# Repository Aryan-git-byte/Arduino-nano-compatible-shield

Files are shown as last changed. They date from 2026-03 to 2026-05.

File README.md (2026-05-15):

# Arduino Nano Compatible Shield

## overview:
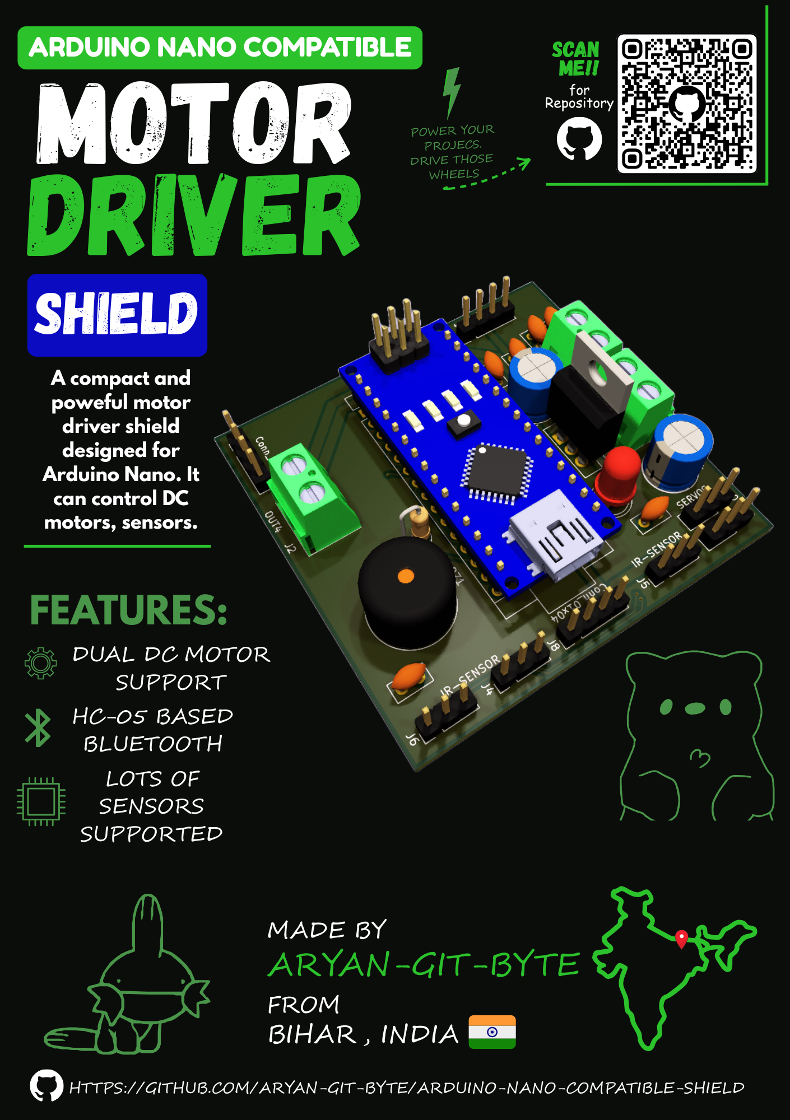
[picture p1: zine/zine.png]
zine

This project is a custom Arduino Nano compatible robotics shield designed to simplify building a 2WD robot car with integrations of many sensors such as ir sensor, ultrasonic, mpu6050 and communication device as bluetooth       
The ultimate goal is to eliminate all those messy wirings , and solderings that we do while making simple 2wd cars packed with features in affordable range.    

## Features:
- U can drive 2 motors with this shield 
- u can integrate 3 ir sensors, 1 ultrasonic sensor, 1 mpu6050, 1 HC-05, and 2 servos

## How to use:
1. insert arduino nano
2. flash the nano with the firmware(change acocrding to your need)
3. connect all the sensors, motors, u need.
4. power the board and operate it

## firmware: Basic firmware written in .ino

## PCB :
### Schematic:
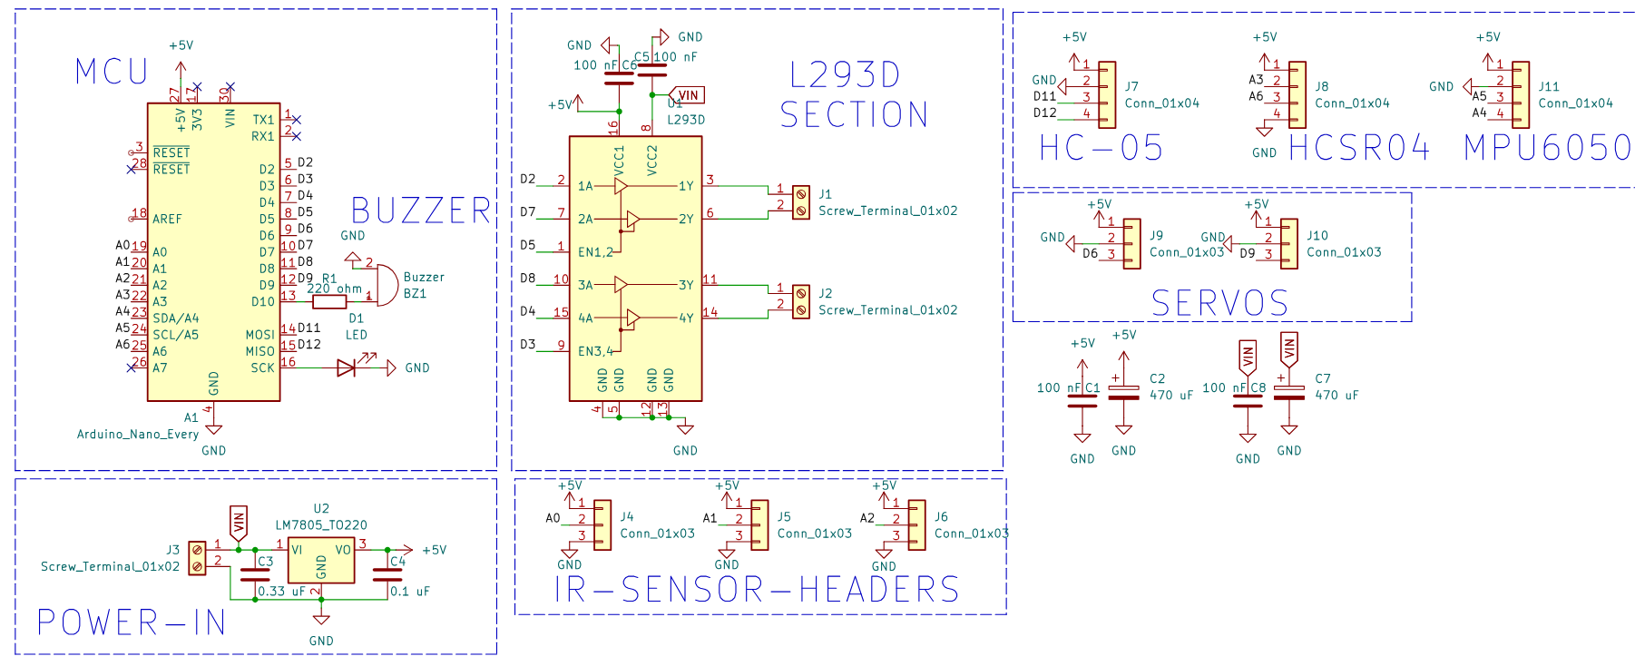
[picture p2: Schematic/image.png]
schematic


### PCB:        
top layer:
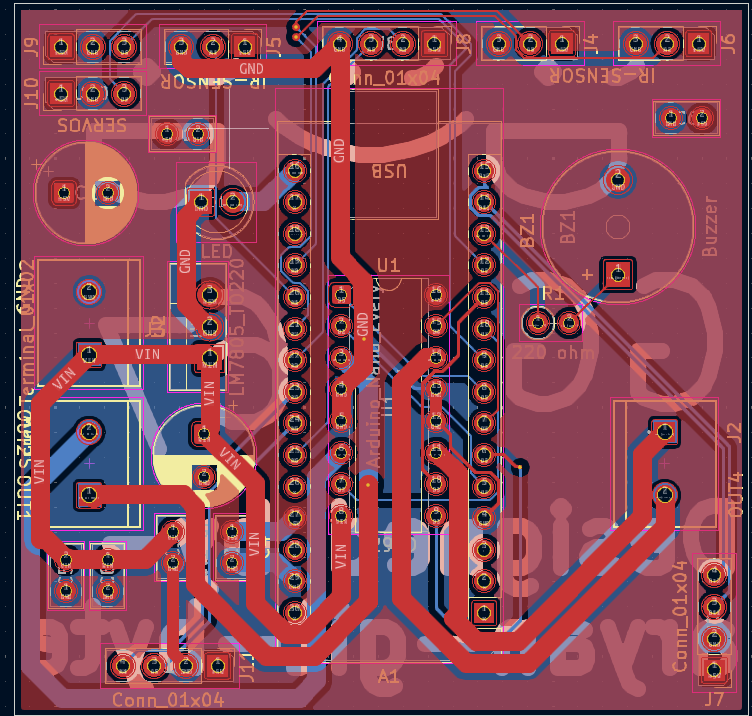
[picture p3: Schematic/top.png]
top
       
bottom layer:       
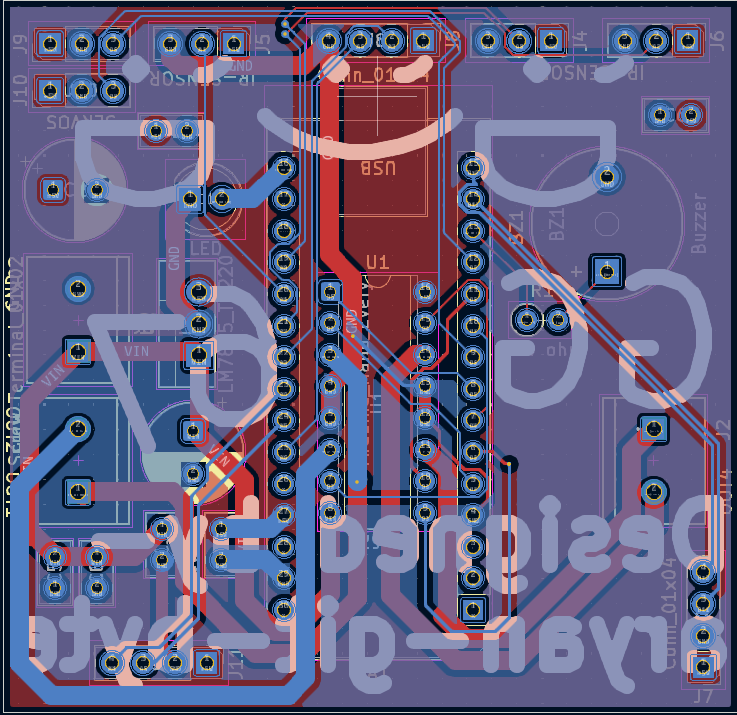
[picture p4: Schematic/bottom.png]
bottom
     
F.silkscreen:       
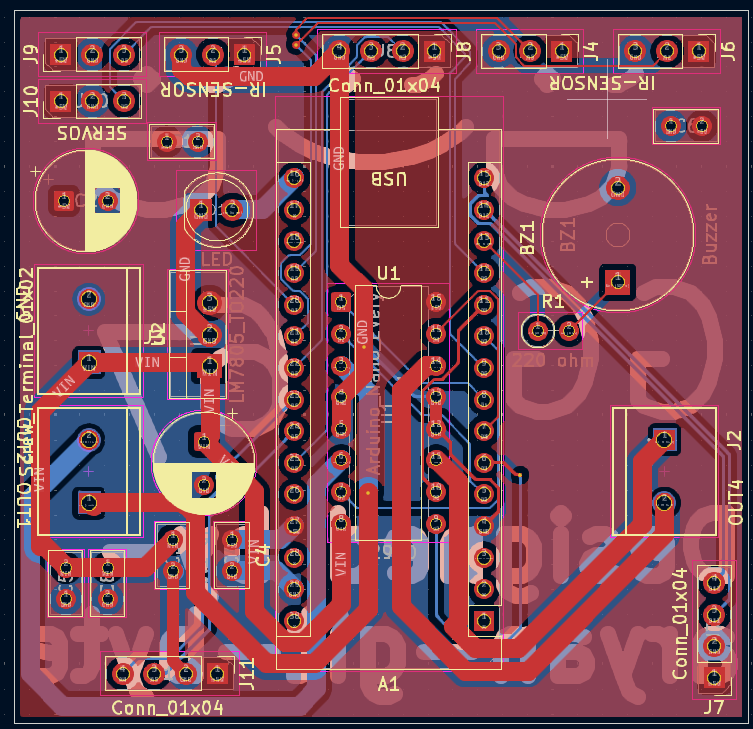
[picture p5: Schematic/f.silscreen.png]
top-silkscreen
    
B.silkscreen:
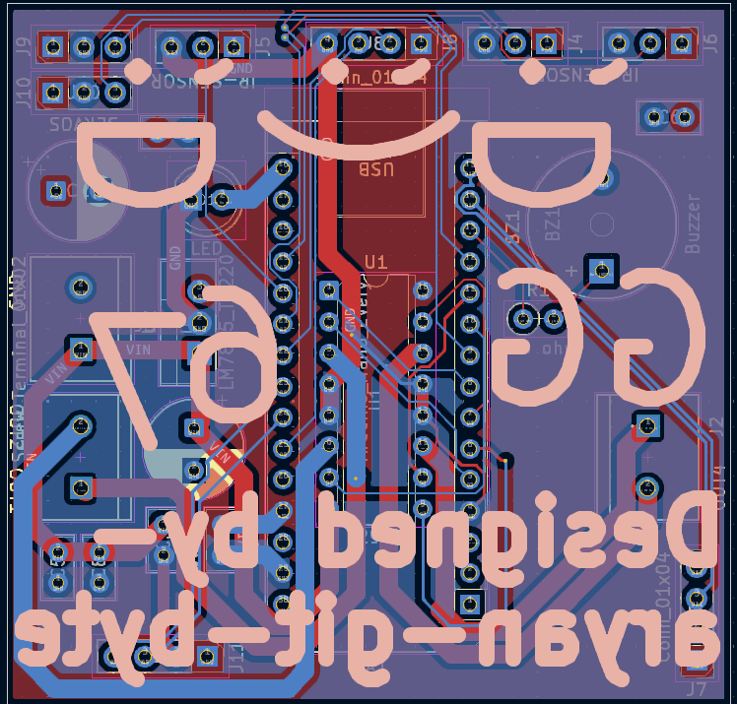
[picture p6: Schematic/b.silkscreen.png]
black-silkscreen

3d:
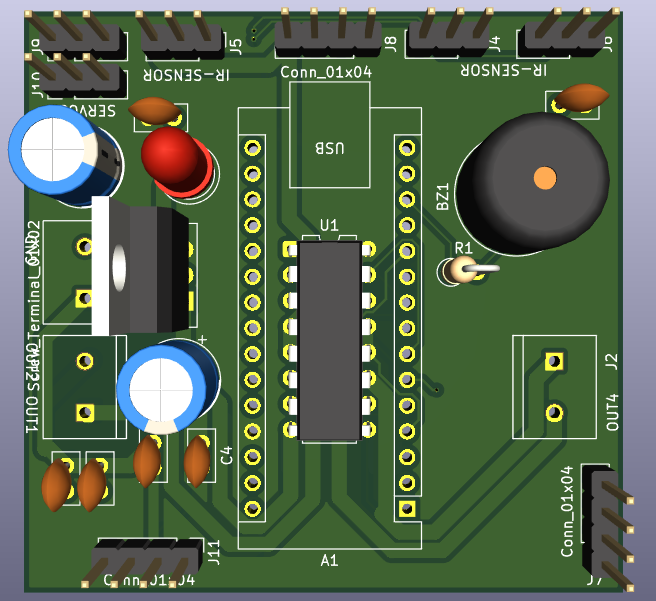
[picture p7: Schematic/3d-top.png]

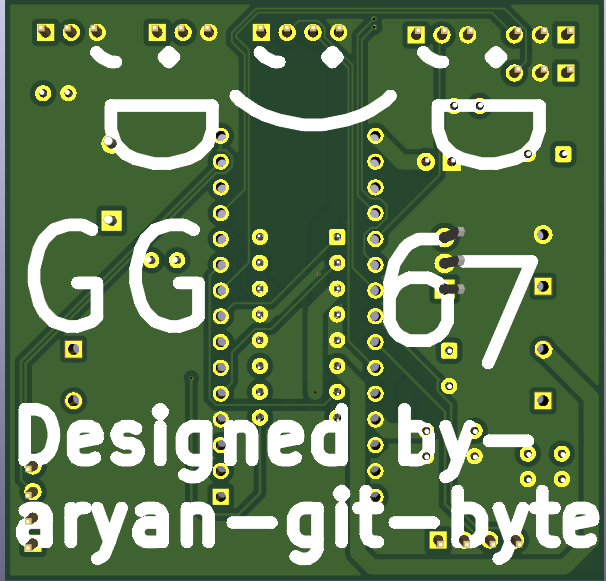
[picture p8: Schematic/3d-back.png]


# Cost Breakdown:

# For the Shield
|item name| quantity | description | link |cost|
|---|---|---|---|----|
|PCB manufacturing(5)|1 |production/gerber.zip|from robu|950 rs (10.33 usd)
|male header x 40|1|for connectors | https://quartzcomponents.com/products/40-pin-break-away-headers-straight-male-headers| 7 rs|
female hedaersx40|2|for arduino nano & conectors| https://quartzcomponents.com/products/40-pin-straight-female-berg-strips| 10 rs|
l293d|1 | motor driver ic | https://quartzcomponents.com/products/l293d-motor-driver-ic| 19 rs|
buzzer|1|buzzzz|https://quartzcomponents.com/products/piezo-buzzer|13 rs|
2 pin screw terminal|3| for motor outputs and power inputs| https://quartzcomponents.com/products/2-pin-pcb-mount-terminal-block-screw-type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| rs 4|
l7805|1|voltage regulator| https://quartzcomponents.com/products/lm7805-5v-positive-regulator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| rs 8 
mini heatsink for l7805| 1| to absorb the heat of the l7805| https://quartzcomponents.com/products/22-15-10mm-black-aluminum-heat-sink-for-to-220-package-power-transistor-cooling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| rs 19|
led|1|for the status| https://quartzcomponents.com/products/red-5mm-led| rs 2
100 nf ceramic| 6| for decoupling | https://quartzcomponents.com/products/10000-pf-0-1uf-ceramic-capacitor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| rs 5
470 uF electrolytic| 2| for safety| https://quartzcomponents.com/products/470-%C2%B5f-25v-radial-electrolytic-capacitor-through-hole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| rs 5

# Assembly overview:
1. get all the parts listed in the BOMs including the chasis, pcb, modules etc.
2. solder them
3. now, start assembling the chasis using this guide:   
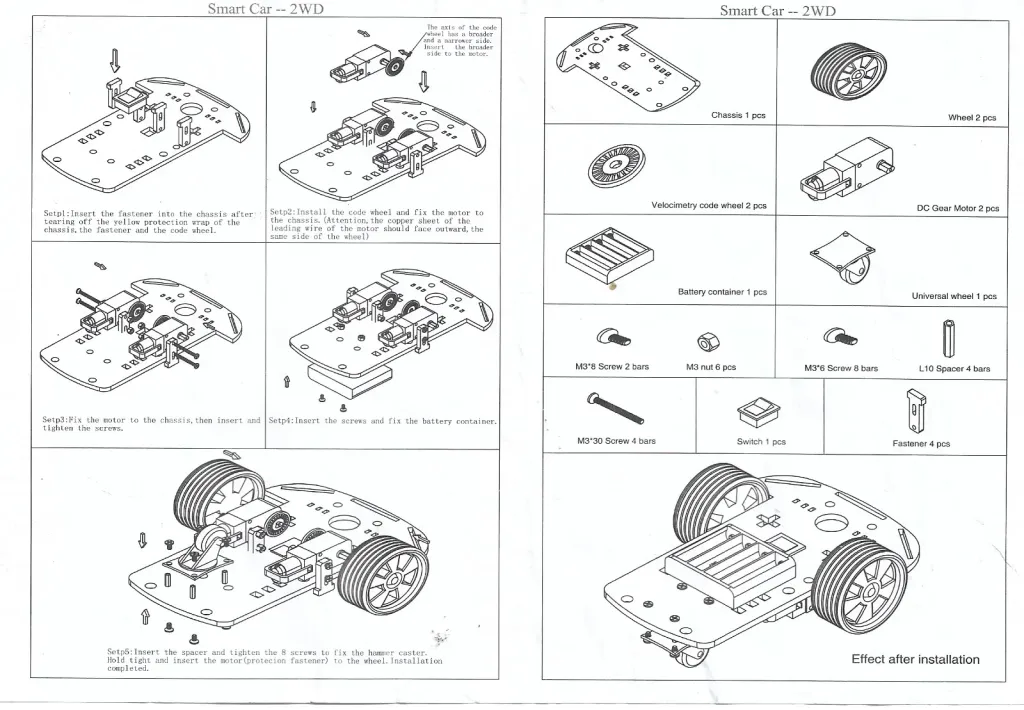
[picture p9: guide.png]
guide

4. now, stick a servo on the front side above the castor wheel and put the ultrasonic mounting bracket on top of it and screw them.
5. now flash the code in `firmware/main.ino`
6. enjoy
## cart: 
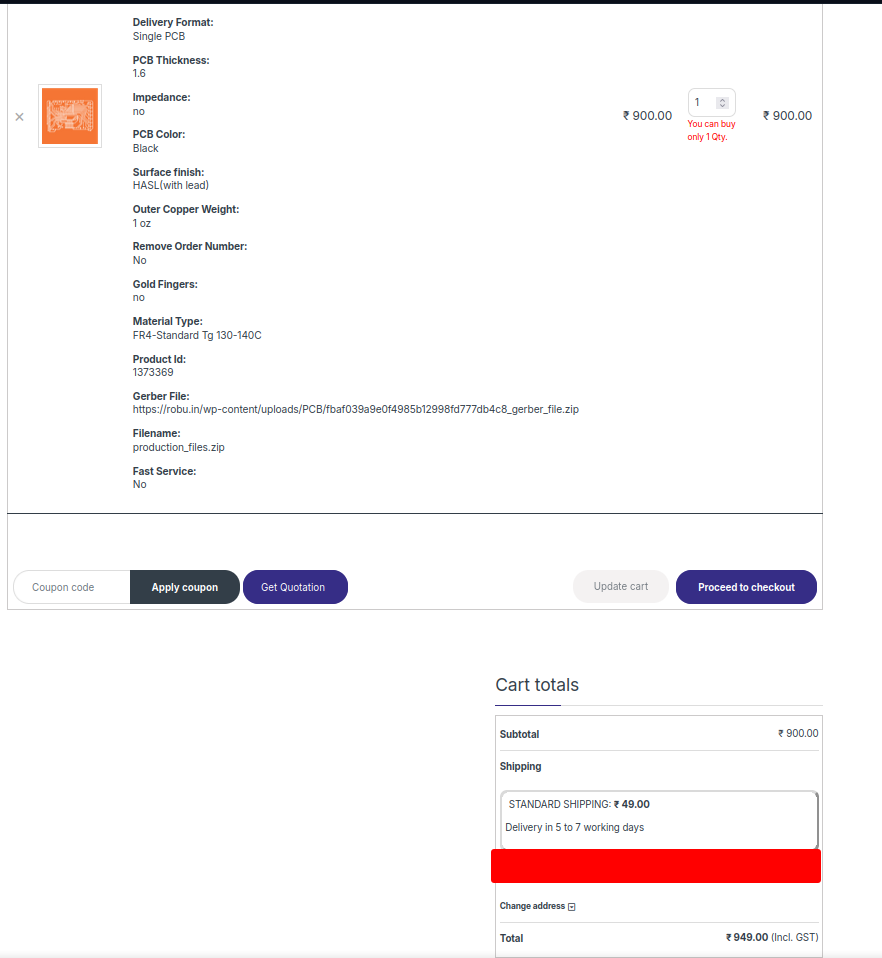
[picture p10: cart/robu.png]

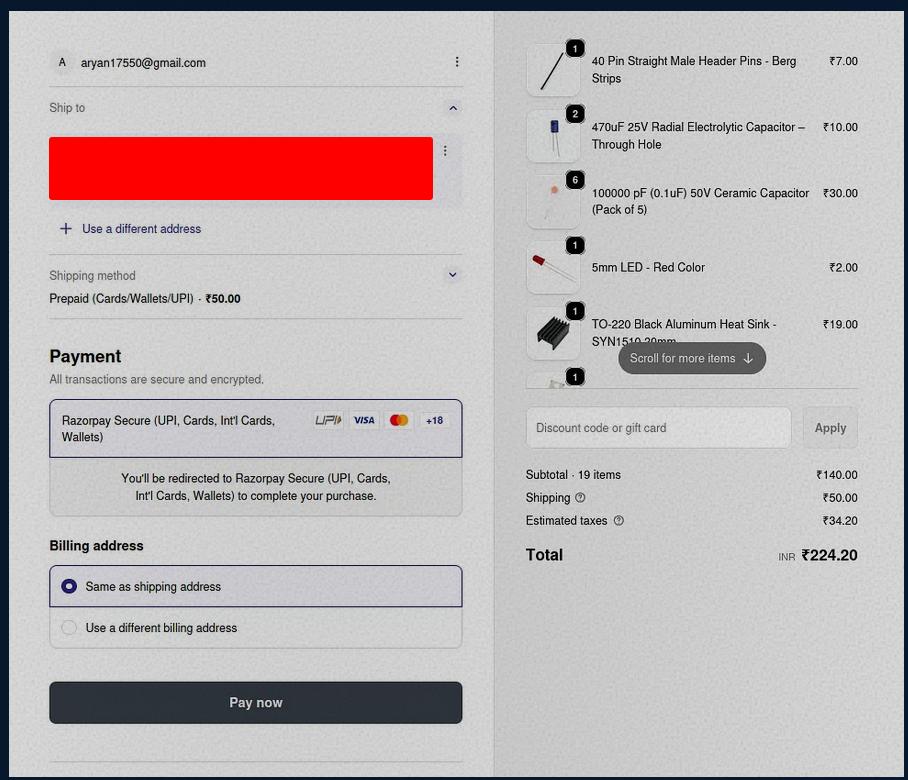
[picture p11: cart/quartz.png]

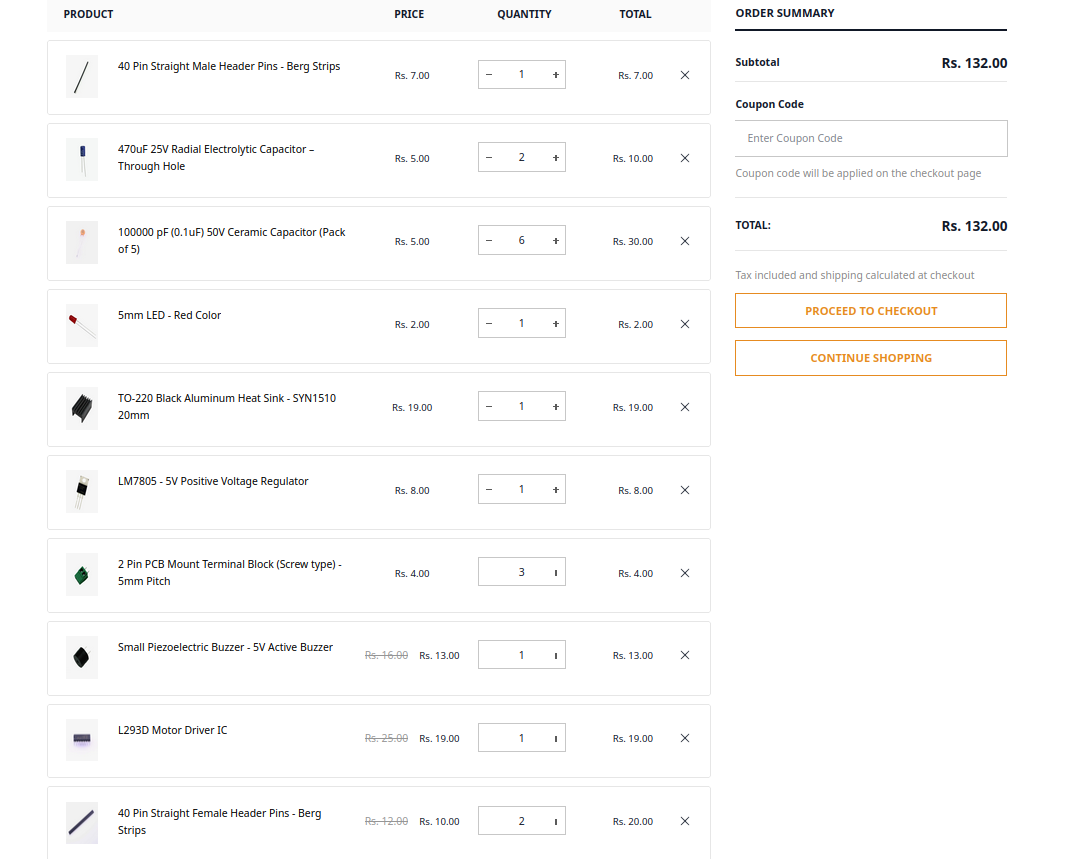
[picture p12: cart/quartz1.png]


## Total(incl. of shipping, gst etc):
### rs 223(2.54 usd) + 950 rs(10.33 usd) = 1173 rs(12.77 usd)
.        
.
# For the 2wd car:

|Item name | quantity| link | price|
|---|---|---|---|
|2wd chasis car set|1|https://robocraze.com/products/2wd-two-wheel-drive-diy-kit-a-smart-robot-car-with-chassis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|rs 289
|servo|1|https://robocraze.com/products/sg90-micro-servo-motor?variant=40192525238425| rs 109
|ir sensor| 3 | https://robocraze.com/products/ir-proximity-sensor-1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| rs 29
|HC-05|1|https://robocraze.com/products/hc-05-bluetooth-module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|rs 224
|HC-SR04|1|https://robocraze.com/products/hc-sr-04-ultrasonic-sensor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|rs 74|
|hc-sr04 mounting bracket| 1 | https://robocraze.com/products/mounting-bracket-for-hc-sr04-ultrasonic-module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| rs 20|
|mpu6050|1|https://robocraze.com/products/mpu-6050-triple-axis-accelerometer-gyroscope-module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|rs 175|

## cart:
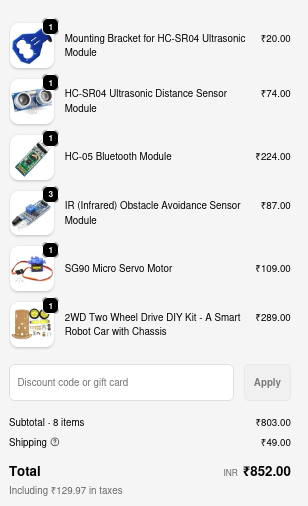
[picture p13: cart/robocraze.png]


## Total = 852 rs for the 2wd car components

# Total(inclduing the pcb, components and shield):
## PCB - 950 rs
## Shield - 223 rs
## component = 852 rs
## Total = 2025 rs(22.01 usd)

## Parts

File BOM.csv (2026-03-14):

Name | Purpose | Cost (USD) | Qty | Total (USD) | Link | Distributor
HC-SR04 | ultrasonic sensor | 0.80 | 1 | 0.80 | https://robocraze.com/products/hc-sr-04-ultrasonic-sensor?variant=40192340983961&country=IN&currency=INR | Robocraze
Robocraze shipping | shipment charge of robocraze | 0.54 | 1 | 0.54 | Link to Listing | robocraze
mpu6050 | to monitor the movement of the car | 1.90 | 1 | 1.90 | https://robocraze.com/products/mpu-6050-triple-axis-accelerometer-gyroscope-module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 | Robocraze
hc-sr04 mounting bracket | to mount the hc-sr04 | 0.22 | 1 | 0.22 | https://robocraze.com/products/mounting-bracket-for-hc-sr04-ultrasonic-module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 | Robocraze
HC-05 | bluetooth module | 2.43 | 1 | 2.43 | https://robocraze.com/products/hc-05-bluetooth-module?variant=40193264189593&country=IN&currency=INR | Robocraze
ir sensor | for multi-purposing the car as line-follower robot too | 0.32 | 3 | 0.96 | https://robocraze.com/products/ir-proximity-sensor-1?variant=40192623640729&country=IN&currency=INR | Robocraze
servo | to mount the ultrasonic | 1.18 | 1 | 1.18 | https://robocraze.com/products/sg90-micro-servo-motor?variant=40192525238425 | Robocraze
2wd chasis car set | to build the car | 3.14 | 1 | 3.14 | https://robocraze.com/products/2wd-two-wheel-drive-diy-kit-a-smart-robot-car-with-chassis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 | Robocraze
Quartz shipping | shipping | 0.91 | 1 | 0.91 | Link to Listing | quartz component
470 uF electrolytic | for safety | 0.05 | 2 | 0.10 | https://quartzcomponents.com/products/470-%C2%B5f-25v-radial-electrolytic-capacitor-through-hole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 | quartz component
100 nf ceramic | for decoupling | 0.05 | 6 | 0.30 | https://quartzcomponents.com/products/10000-pf-0-1uf-ceramic-capacitor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 | quartz component
led | for the status | 0.02 | 1 | 0.02 | https://quartzcomponents.com/products/red-5mm-led | quartz component
mini heatsink for l7805 | to absorb the heat of the l7805 | 0.21 | 1 | 0.21 | https://quartzcomponents.com/products/22-15-10mm-black-aluminum-heat-sink-for-to-220-package-power-transistor-cooling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 | quartz component
l7805 | voltage regulator | 0.09 | 1 | 0.09 | https://quartzcomponents.com/products/lm7805-5v-positive-regulator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 | quartz component
2 pin screw terminal | for motor outputs and power inputs | 0.04 | 3 | 0.12 | https://quartzcomponents.com/products/2-pin-pcb-mount-terminal-block-screw-type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 | quartz component
buzzer | buzzzz | 0.14 | 1 | 0.14 | https://quartzcomponents.com/products/piezo-buzzer | quartz component
l293d | motor driver ic | 0.21 | 1 | 0.21 | https://quartzcomponents.com/products/l293d-motor-driver-ic | quartz component
female hedaersx40 | for arduino nano & conectors | 0.11 | 2 | 0.22 | https://quartzcomponents.com/products/40-pin-straight-female-berg-strips | quartz component
male header x 40 | for connectors | 0.08 | 1 | 0.08 | https://quartzcomponents.com/products/40-pin-break-away-headers-straight-male-headers | quartz component
PCB manufacturing(5) + shipping (robu) | to get the pcb manufactured | 10.33 | 1 | 10.33 | production/gerber.zip | Robu.in

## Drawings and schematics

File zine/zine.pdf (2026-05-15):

## ARDUINO NANO COMPATIBLE

# MOTOR

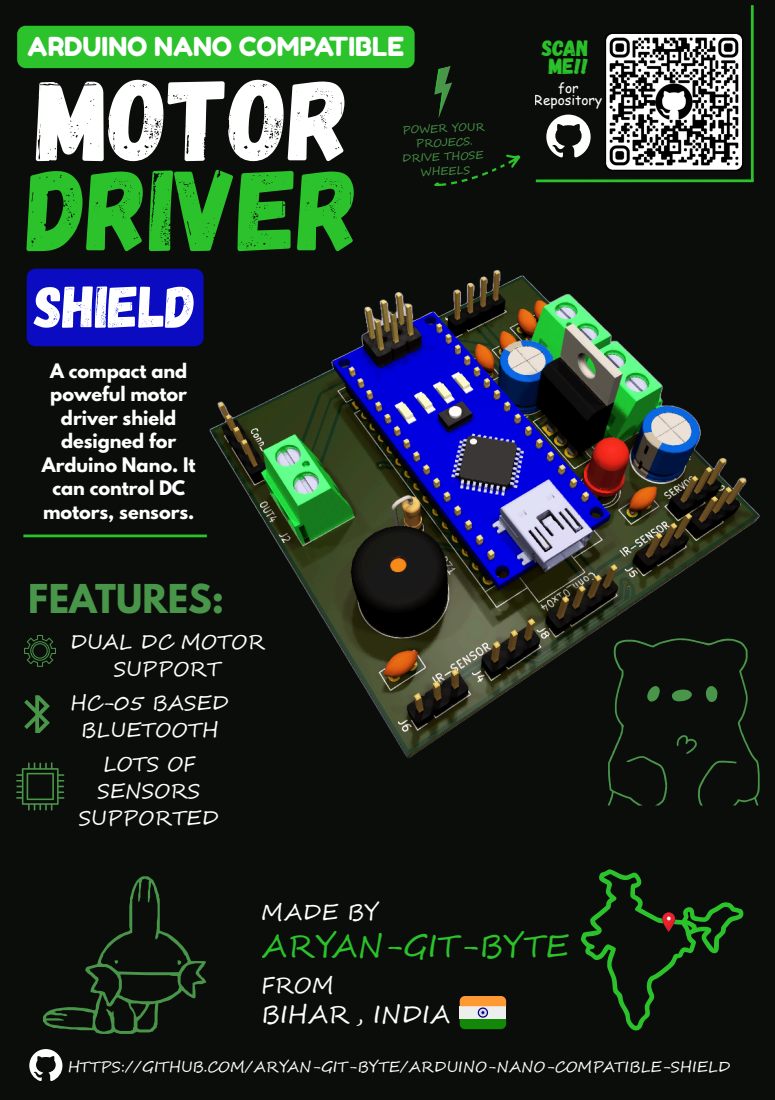
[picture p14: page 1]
DRIVER; SHIELD; scan me!! for Repository; POWER YOUR PROJECS. DRIVE THOSE WHEELS

A compact and
poweful motor
driver shield
designed for
Arduino Nano. It
can control DC
motors, sensors.
FEATURES:
DUAL DC MOTOR
SUPPORT
HC-05 BASED
BLUETOOTH
LOTS OF
SENSORS
SUPPORTED

MADE BY
ARYAN-GIT-BYTE
FROM
BIHAR , INDIA

HTTPS://GITHUB.COM/ARYAN-GIT-BYTE/ARDUINO-NANO-COMPATIBLE-SHIELD

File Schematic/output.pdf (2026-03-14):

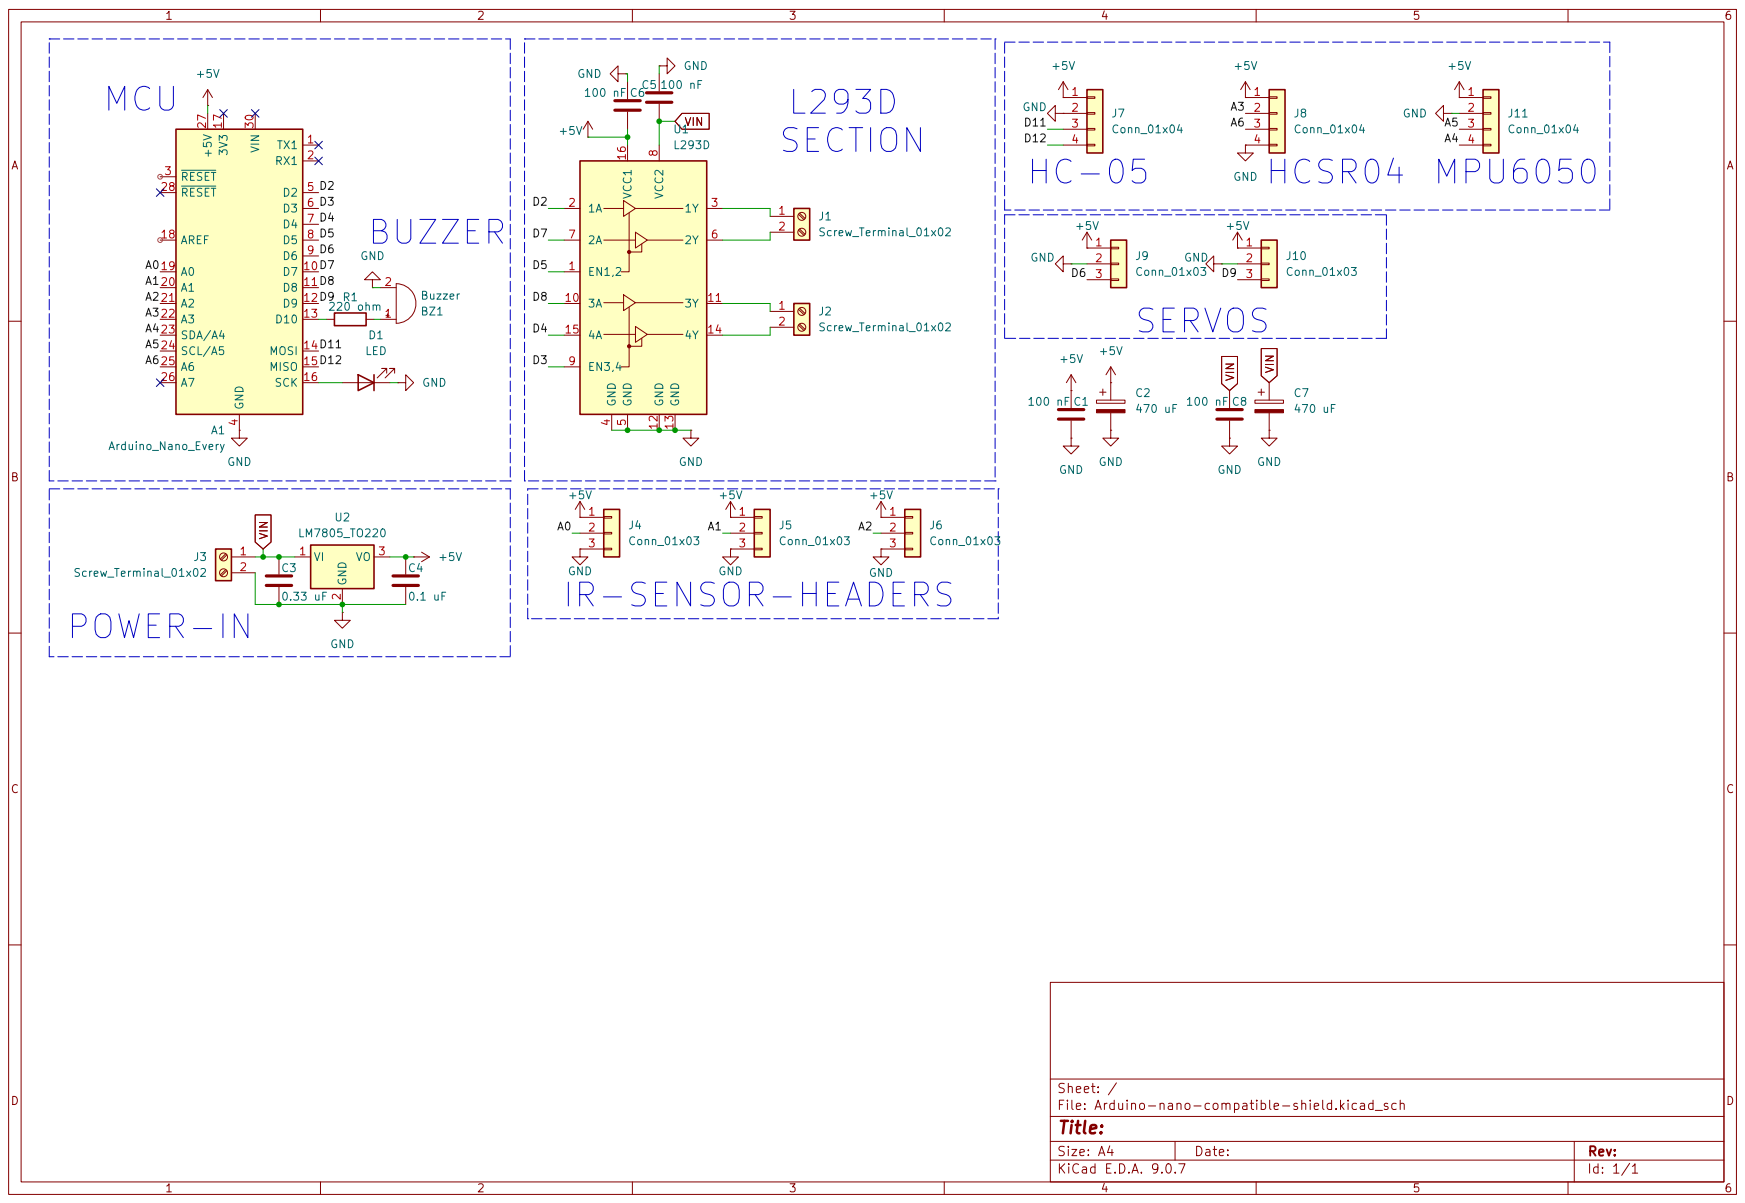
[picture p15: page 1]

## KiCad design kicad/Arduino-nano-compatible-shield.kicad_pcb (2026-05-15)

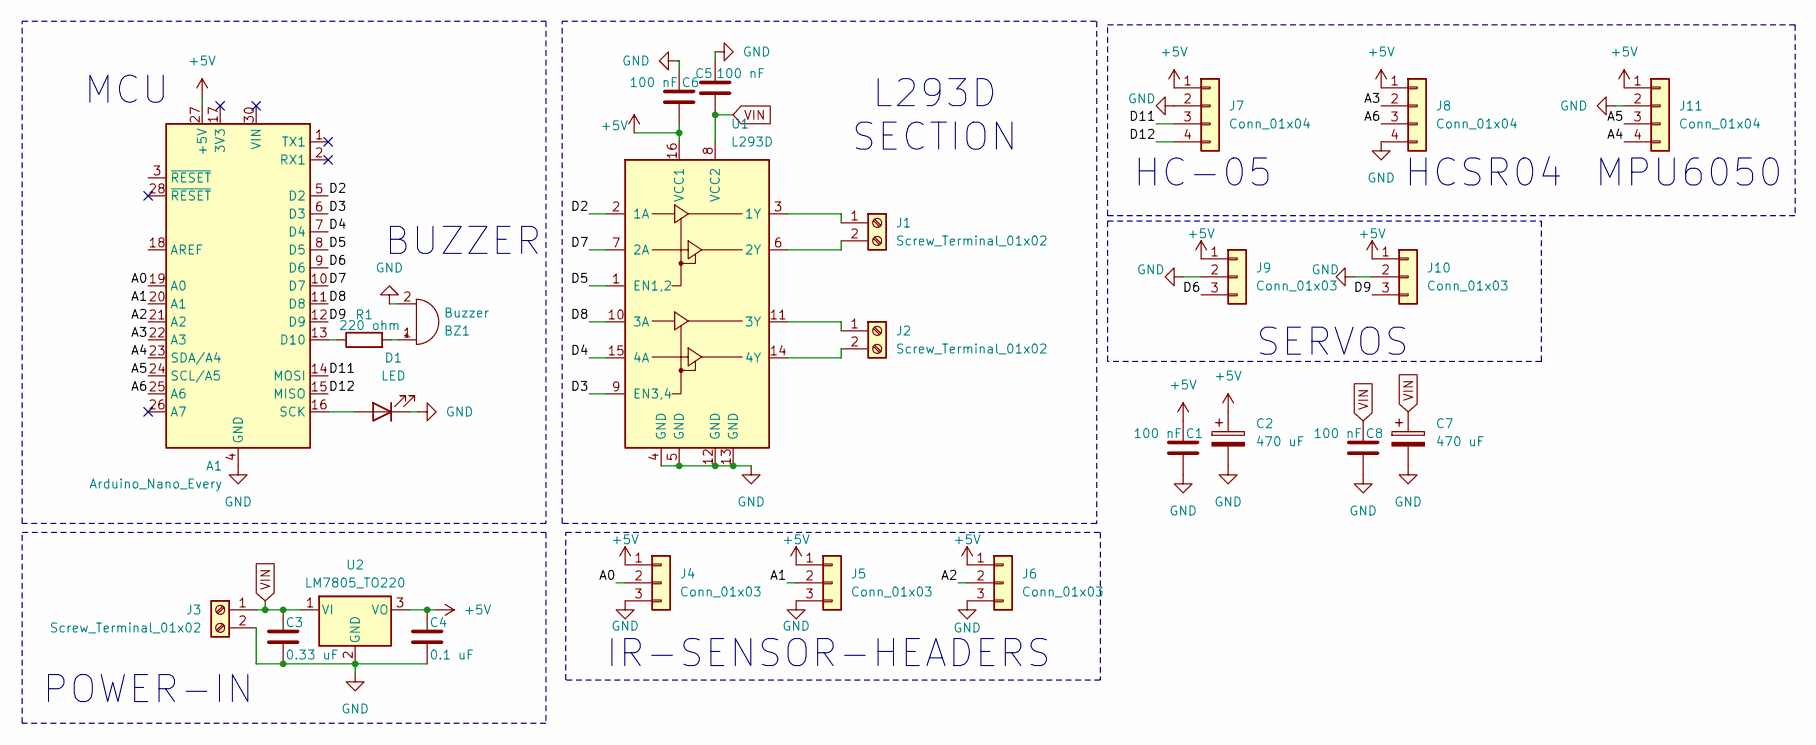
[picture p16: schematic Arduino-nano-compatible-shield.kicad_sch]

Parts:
A1: Arduino_Nano_Every; Arduino_Nano
BZ1: Buzzer; Buzzer_12x9.5RM7.6
C1, C5, C6, C8: 100 nF; C_Disc_D5.0mm_W2.5mm_P2.50mm
C2, C7: 470 uF; CP_Radial_D8.0mm_P3.50mm
C3: 0.33 uF; C_Disc_D5.0mm_W2.5mm_P2.50mm
C4: 0.1 uF; C_Disc_D5.0mm_W2.5mm_P2.50mm
D1: LED; LED_D5.0mm
J1, J2, J3: Screw_Terminal_01x02; TE_282837-2
J4, J5, J6, J9, J10: Conn_01x03; PinHeader_1x03_P2.54mm_Vertical
J7, J8, J11: Conn_01x04; PinHeader_1x04_P2.54mm_Vertical
R1: 220 ohm; R_Axial_DIN0207_L6.3mm_D2.5mm_P2.54mm_Vertical
U1: L293D; DIP-16_W7.62mm
U2: LM7805_TO220; TO-220-3_Vertical

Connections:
+5V: A1.27 (+5V), C1.1, C2.1, C4.1, C6.2, J4.1, J5.1, J6.1, J7.1, J8.1, J9.1, J10.1, J11.1, U1.16 (VCC1), U2.3 (VO)
/A0: A1.19 (A0), J4.2
/A1: A1.20 (A1), J5.2
/A2: A1.21 (A2), J6.2
/A3: A1.22 (A3), J8.2
/A4: A1.23 (SDA/A4), J11.4
/A5: A1.24 (SCL/A5), J11.3
/A6: A1.25 (A6), J8.3
/D2: A1.5 (D2), U1.2 (1A)
/D3: A1.6 (D3), U1.9 (EN3,4)
/D4: A1.7 (D4), U1.15 (4A)
/D5: A1.8 (D5), U1.1 (EN1,2)
/D6: A1.9 (D6), J9.3
/D7: A1.10 (D7), U1.7 (2A)
/D8: A1.11 (D8), U1.10 (3A)
/D9: A1.12 (D9), J10.3
/D11: A1.14 (MOSI), J7.3
/D12: A1.15 (MISO), J7.4
GND: A1.4 (GND), A1.29 (GND), BZ1.2 (-), C1.2, C2.2, C3.2, C4.2, C5.1, C6.1, C7.2, C8.2, D1.1 (K), J3.2, J4.3, J5.3, J6.3, J7.2, J8.4, J9.2, J10.2, J11.2, U1.4 (GND), U1.5 (GND), U1.12 (GND), U1.13 (GND), U2.2 (GND)
unnamed: A1.13 (D10), R1.1
unnamed: A1.16 (SCK), D1.2 (A)
unnamed: BZ1.1 (+), R1.2
unnamed: J1.1, U1.3 (1Y)
unnamed: J1.2, U1.6 (2Y)
unnamed: J2.1, U1.11 (3Y)
unnamed: J2.2, U1.14 (4Y)
VIN: C3.1, C5.2, C7.1, C8.1, J3.1, U1.8 (VCC2), U2.1 (VI)

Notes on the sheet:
L293D SECTION
MPU6050
MCU
HC-05
HCSR04
SERVOS
POWER-IN
IR-SENSOR-HEADERS
BUZZER

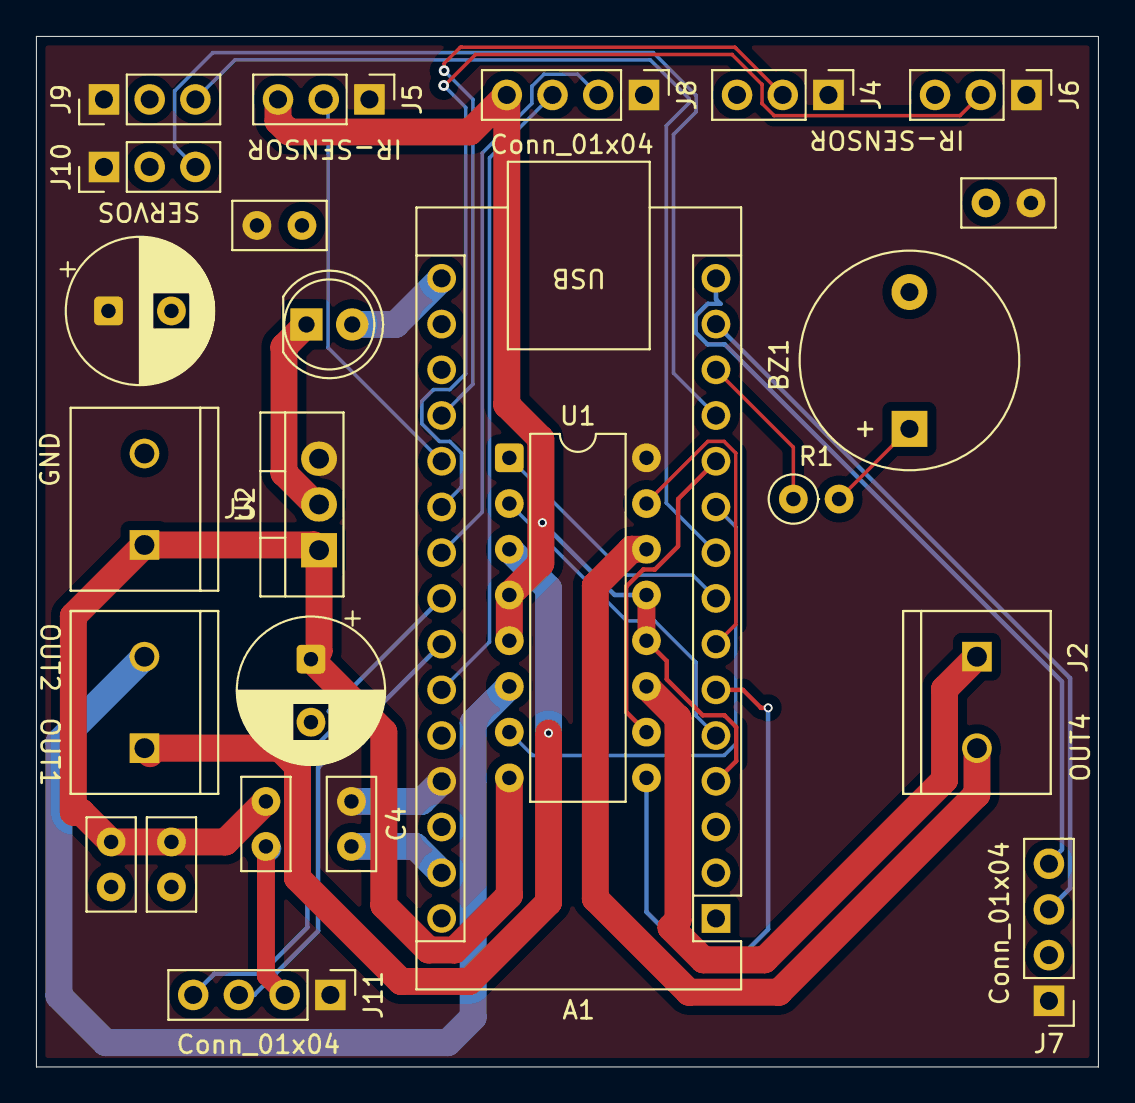
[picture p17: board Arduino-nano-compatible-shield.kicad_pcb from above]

Board: 2 copper layers, 59.0 x 57.2 mm, 25 parts (0 on the bottom side), 27 nets.

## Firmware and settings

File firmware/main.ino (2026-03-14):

#include <Servo.h>
#include <SoftwareSerial.h>
#include <Wire.h>


Servo myservo;
SoftwareSerial bt(12, 11);
unsigned long lastStream = 0;


void moveForward() {
    digitalWrite(2, HIGH);
    digitalWrite(7, LOW);
    digitalWrite(8, HIGH);
    digitalWrite(4, LOW);
    analogWrite(5, 200);
    analogWrite(3, 200);
}

void moveBackward(){
    digitalWrite(7, HIGH);
    digitalWrite(2, LOW);
    digitalWrite(4, HIGH);
    digitalWrite(8, LOW);
    analogWrite(5, 200);
    analogWrite(3, 200);
}

void turnLeft(){
    digitalWrite(2, HIGH);
    digitalWrite(7, LOW);
    digitalWrite(4, HIGH);
    digitalWrite(8, LOW);
    analogWrite(5, 200);
    analogWrite(3, 200);
}

void turnRight(){
    digitalWrite(7, HIGH);
    digitalWrite(2, LOW);
    digitalWrite(8, HIGH);
    digitalWrite(4, LOW);
    analogWrite(5, 200);
    analogWrite(3, 200);
}

void stopmotors(){
    analogWrite(5, 0);
    analogWrite(3, 0);
    digitalWrite(2, LOW);
    digitalWrite(4, LOW);
    digitalWrite(7, LOW);
    digitalWrite(8, LOW);
}

void scanLeft(){
    myservo.write(30);
}

void scanRight(){
    myservo.write(150);
}

void scanCentre(){
    myservo.write(90);
}

void bluetooth(){
    if (bt.available()) {
        char cmd = bt.read();
        switch (cmd) {
            case 'F' : moveForward(); break;
            case 'B': moveBackward(); break;
            case 'L': turnLeft();     break;
            case 'R': turnRight();    break;
            case 'S': stopmotors();   break;
        }
    }
}

long getDistance() {
  digitalWrite(A3, LOW);
  delayMicroseconds(2);
  digitalWrite(A3, HIGH);
  delayMicroseconds(10);       
  digitalWrite(A3, LOW);

  long duration = pulseIn(A6, HIGH, 25000);
  if (duration == 0) return -1;  
  return duration / 58;          
}

void readMPU(int &ax, int &ay, int &az,
             int &gx, int &gy, int &gz,
             float &temp) {
    Wire.beginTransmission(0x68);
    Wire.write(0x3B);             
    Wire.endTransmission(false);
    Wire.requestFrom(0x68, 14);   

    ax = (Wire.read() << 8) | Wire.read();
    ay = (Wire.read() << 8) | Wire.read();
    az = (Wire.read() << 8) | Wire.read();
    int rawTemp = (Wire.read() << 8) | Wire.read();
    gx = (Wire.read() << 8) | Wire.read();
    gy = (Wire.read() << 8) | Wire.read();
    gz = (Wire.read() << 8) | Wire.read();
    temp = rawTemp / 340.0 + 36.53;
}

void setup()
{
    pinMode(2, OUTPUT);
    pinMode(7, OUTPUT);
    pinMode(8, OUTPUT);
    pinMode(4, OUTPUT);
    pinMode(5, OUTPUT);
    pinMode(3, OUTPUT);
    myservo.attach(6);
    pinMode(A3, OUTPUT);
    pinMode(A6, INPUT);
    pinMode(A0, INPUT);
    pinMode(A1, INPUT);
    pinMode(A2, INPUT);
    Serial.begin(9600);
    bt.begin(9600);
    Wire.begin();
    Wire.beginTransmission(0x68);
    Wire.write(0x6B);
    Wire.write(0);
    Wire.endTransmission(true);
    

}
void loop(){
    bluetooth();
    int irfrontleft  = analogRead(A0);
    int irfrontright = analogRead(A1);
    int irback       = analogRead(A2);
    if (irfrontleft < 500 && irfrontright < 500) {
        stopmotors();
    } else if (irfrontleft < 500) {
        turnRight();
        delay(400);
        stopmotors();
    } else if (irfrontright < 500) {
        turnLeft();
        delay(400);
        stopmotors();
    }
    scanCentre();
    long distcenter = getDistance();
    if (distcenter < 20) {
        stopmotors();
        delay(100);

        scanLeft();
        delay(300);
        long distleft = getDistance();
        delay(300);

        scanRight();
        delay(300);
        long distright = getDistance();
        delay(300);

        scanCentre();
        delay(200);

        if (distleft < 20 && distright < 20) {
            if (irback < 500) {
                stopmotors();
            } else {
                moveBackward();
                delay(3000);
                stopmotors();
            }
        }
        else if (distleft > distright) {
            turnLeft();
            delay(400);
            stopmotors();
        }
        else{
            turnRight();
            delay(400);
            stopmotors();
        }
    }
    else {
        moveForward();
    }

    if (millis() - lastStream > 500) {
    lastStream = millis();
    int ax, ay, az, gx, gy, gz;
    float temp;
    readMPU(ax, ay, az, gx, gy, gz, temp);
    bt.print("AX:"); bt.print(ax);
    bt.print(" AY:"); bt.print(ay);
    bt.print(" AZ:"); bt.print(az);
    bt.print(" GX:"); bt.print(gx);
    bt.print(" GY:"); bt.print(gy);
    bt.print(" GZ:"); bt.print(gz);
    bt.print(" TMP:"); bt.println(temp);
}


}
